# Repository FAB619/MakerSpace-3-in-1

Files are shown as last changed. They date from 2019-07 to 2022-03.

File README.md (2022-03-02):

<div align="center"><h1 style="font-family: courier;" align="center">MakerSpace 3-in-1</h1></div>

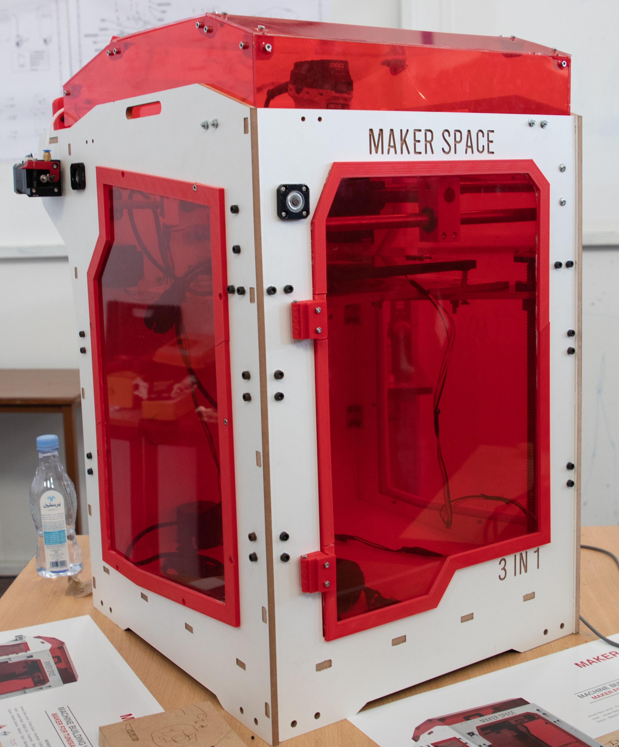
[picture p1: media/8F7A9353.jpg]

<div align="center"><i>Open Source 3-in-1 fabrication machine</i></div>

# Hello World 
# Premises

3D printers are amazing. Unfortunately, they used to be hulking, complicated, expensive, and with limited functions. We’ve been hearing about and experiencing the pain of setting up the difficult-to-use DIY 3D printer kit and being limited by the standard plug-and-play 3D printer. We are hoping to change that. So we came up with an idea: create a 3D printer, which is easy-to-use, expandable for makers, and truly affordable for everyone.

That’s why we designed MakerSpace to be all-in-one.
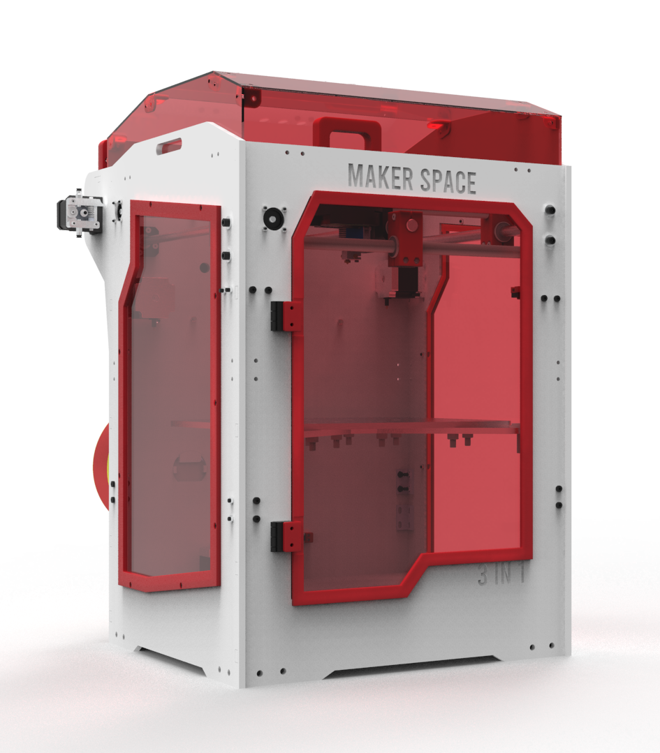
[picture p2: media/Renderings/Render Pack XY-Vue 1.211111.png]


# MakerSpace 3-in-1
MakerSpace is a Combination of 3 machines which characterizes any maker space or fablab around the word,Powerfull tool for rapid prototyping. Designed for Makers, Desingers, Architects ...

 MakerSpace has been developed using standard [Fab Lab equipment](https://docs.google.com/spreadsheets/d/1U-jcBWOJEjBT5A0N84IUubtcHKMEMtndQPLCkZCkVsU/pub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) and [technique](http://fab.academany.org/2019/schedule.html). MakerSpace was built in [FabLab ENIT](https://www.facebook.com/FabLabENIT/) by Kais Alila and the help of a lot of people (Desingers & Engineers).

 MakerSpace brings the advantages of an open source development:

- full awareness about how FabLab machines works
- reproducible design
- possibility to customize the machine and/or to build new ones
- local self-fixing and self-production of the machine parts
- community can use and improve the design
- cheap alternative to have a desktop FabLab
- use MakerSpace as tool for prototyping

Moreover, It's also a desktop makerspace, a combination of 3D printer, laser engraver, and CNC machine with interchangeable heads. Using FDM (Fused Deposition Modeling), it uses standard 1.75mm 3D printer filament with common [e3d v6](https://e3d-online.com/) extruder, 2 watt Laser module with TTl driver usefull for cutting and engraving on paper, cardbord, 3mm MDF and plexiglass and 500 watt spindle for molding and casting, making pcbs and cutting wood.

MakerSpace was designed starting from two major problems:
-Space factor: With makerspace we are replacing 3 machines so we gain have more space.
-Cost factor: With all-in-one machines we are saving money
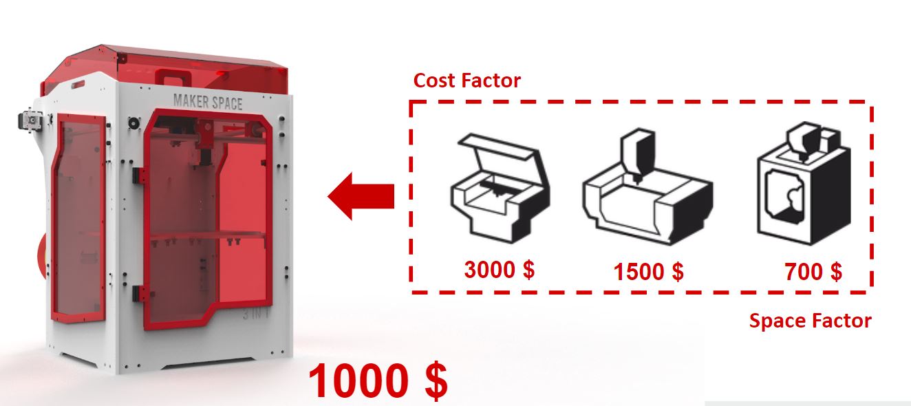
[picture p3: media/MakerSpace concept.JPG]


# Specifications
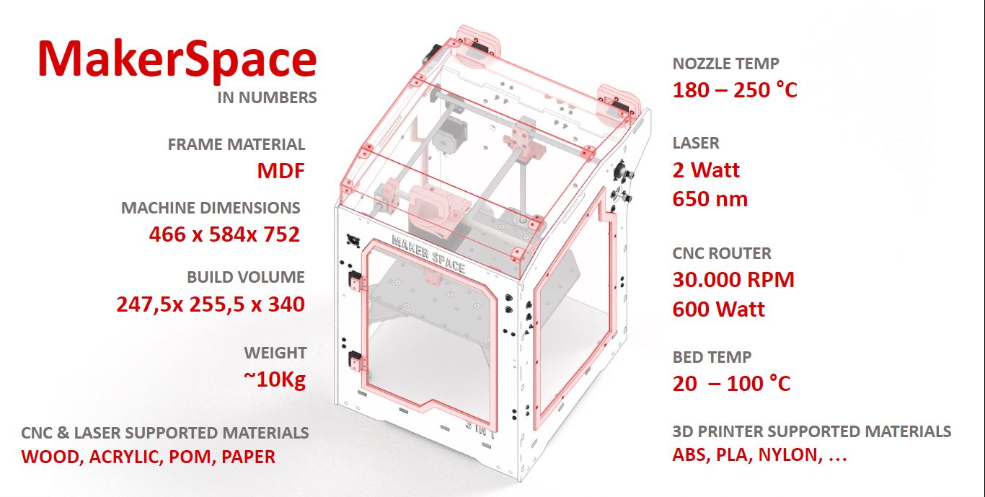
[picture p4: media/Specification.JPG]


**MakerSpace specifications**:

- **466mm x 544mm x 752mm** machine dimension
- **247.5mm x 255.5mm x 340mm** working area
- **3 Tools** with interchangeble tools
- **1.75mm** filament
- **0.1 - 0.6mm** nozzle size
- **NEMA 17-23**  stepper motors
- **BallScrews SFU 1204**
- stages with **linear stainless steel rod guides**
- **Wood frame**
- **heated bed**
- **closed housing** of acrylic (enclouser)
- **2 watt 405nm Laser** module with TTL driver
- **30000 Rpm 500 watt** CNC router (Spindle)
- fabbable **Arduino Mega & Ramps and A4988 stepper driver** based electronics
- **Electronics resolution** 6 microns
- PSU 12V 15A
- printing from **USB** drive
- **Materials**:

    -Plastics: PLA, Flex, ABS, Acetal, Acrylic, PVC…

    -Woods: Oak, Maple, Hickory, Walnut…

    -And much more!
- BOM cost of about **1000€**
- power requirements 220V

# Customizable
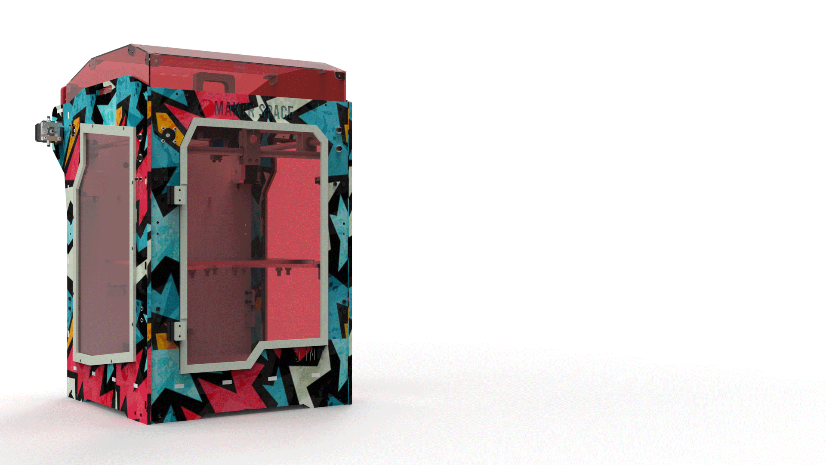
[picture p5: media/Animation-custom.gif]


# Tools
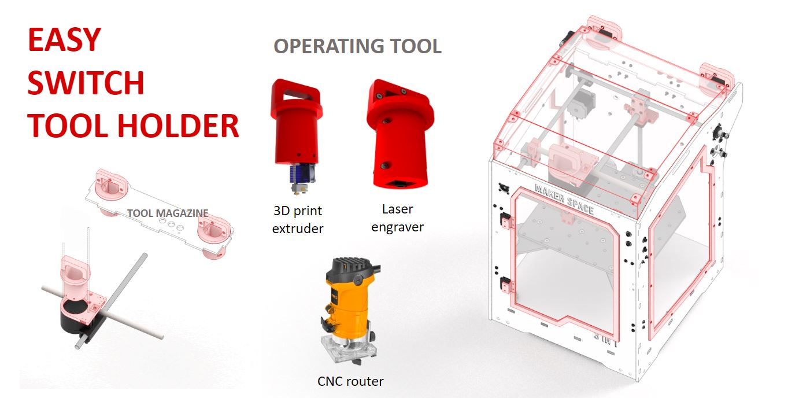
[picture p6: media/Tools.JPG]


# Everything is 3D printed
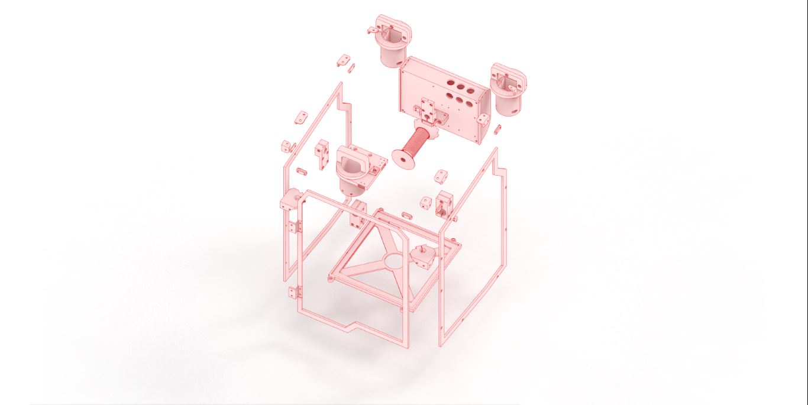
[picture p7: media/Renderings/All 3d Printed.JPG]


To guarantee the reproducibility of MakerSpace, the majority of the parts are 3D printed in Fab Lab. It took approximately 140 hours print, and 2 kilogramms PLA filament. All the parts are designed with solidworks and Simplify3D for generating the g-code. The spool holder is an open source design designed by [Undeviljur](https://www.thingiverse.com/Undeviljur/about) and this is the thingiverse link:

https://www.thingiverse.com/thing:1546811

This is the table for [3D printed Parts](https://github.com/Fab-Lab-Machines/MakerSpace-3-in-1/tree/master/Fabrication/3D%20printing)

|désignation |nombre|build time (hour:minute)|plastic weight (g)|lenght (mm)| |
|---|---|---|---|---|---|
|Box base |1 |13:14:00 |175,15 |5840 | |
|Box-top |2 |18:46:00 |194,86 |64812,3 | |
|Eceres |10 |3:17:00 |31,31 |10412,6 | |
|extruder housing |1 |15:39:00 |254,32 |84588,4 |with support|
|FF_housing |1 |2:14:00 |26,91 |8949,7 |with support|
|Frame-protection-power |2 |6:23:00 |80,49 |26772,2 | |
|Front protection frame |1 |7:14:00 |96,78 |32188,5 | |
|hinge |4 |1:41:00 |16,45 |5472,4 | |
|Laser-housing 1st |1 |7:05:00 |80,07 |26632,7 |with support|
|Laser-housing second |1 |7:06:00 |80,07 |26629,8 |with support|
|LMF_16UU costum |2 |5:00:00 |39,65 |13187,5 | |
|Mors-mobile-extruder |1 |0:41:00 |7,02 |2335 |with support|
|Rod support |1 |1:28:00 |16,02 |5327,7 | |
|Rod support 2 |2 |2:59:00 |32,36 |10762,6 | |
|Spacer_5_10 |4 |0:20:00 |2,25 |746,9 | |
|Support bed & Glass |1 |10:06:00 |121,82 |40517 | |
|support end stop |2 |0:27:00 |4,42 |1470,5 | |
|Support FF For SFU1 |2 |2:02:00 |21 |6985 | |
|Support on Hinge |2 |1:23:00 |14,73 |4899,1 | |
|Support Rod Bottom |2 |3:04:00 |33,01 |10979 | |
|Spool Holder  (all parts)|1 |10:46:00 |123,32 |41015 |with support|
|Tool holder |1 |16:48:00 |191,99 |63855,4 | |
|Tool holder Top |1 |3:51:00 |43,46 |14421,6 | |
|Total : |46 |141:40:00 |1687,46 |508800,9 |

# CNC Milling
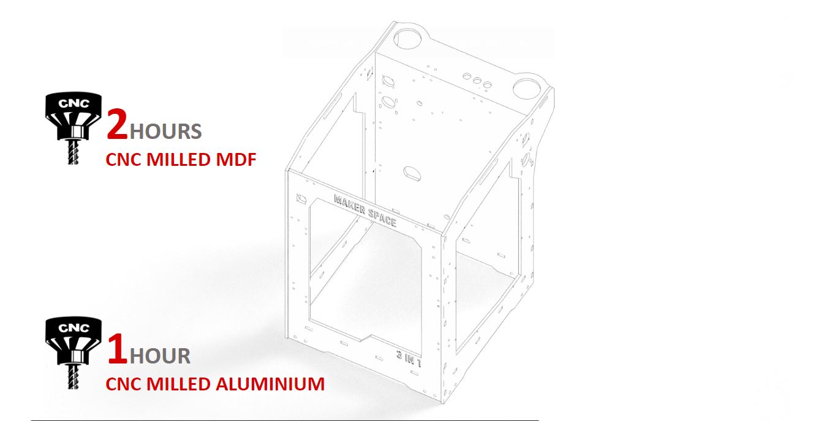
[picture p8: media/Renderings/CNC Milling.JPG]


# Metal parts
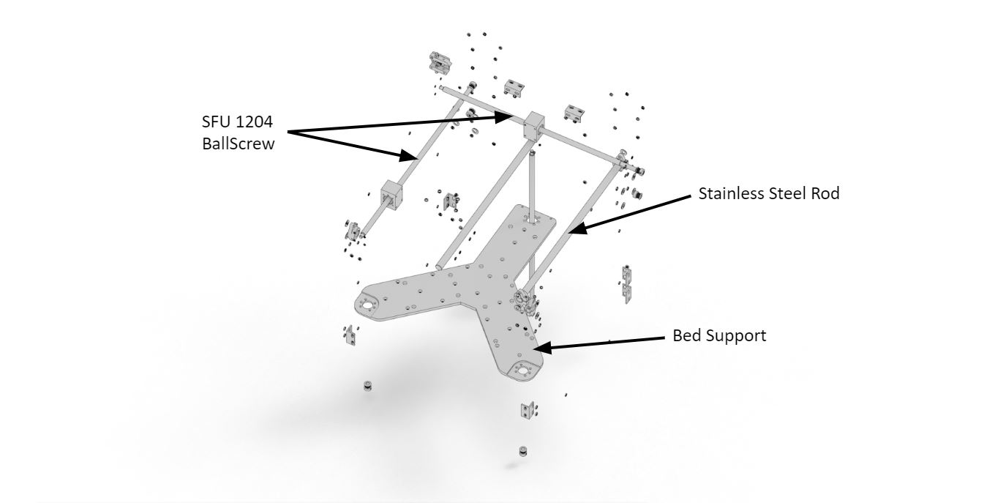
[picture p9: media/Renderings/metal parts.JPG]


# Electronics
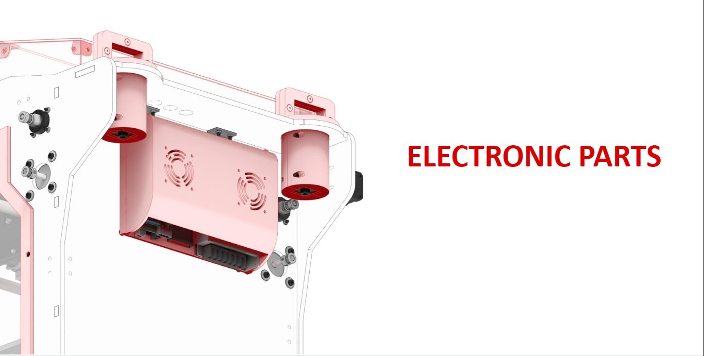
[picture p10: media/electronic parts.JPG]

<div align="center"><i>Electronic Box</i></div>
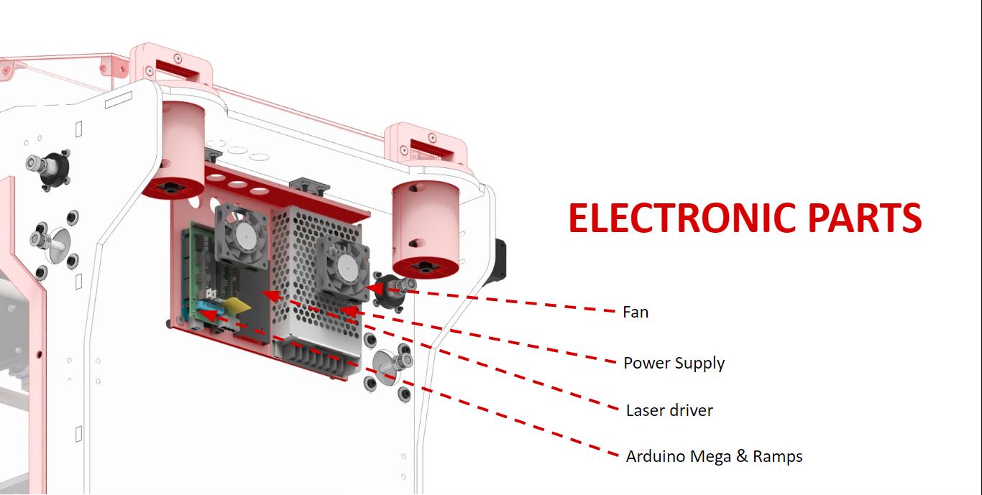
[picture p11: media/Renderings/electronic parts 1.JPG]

<div align="center"><i>Components</i></div>

# Compact design
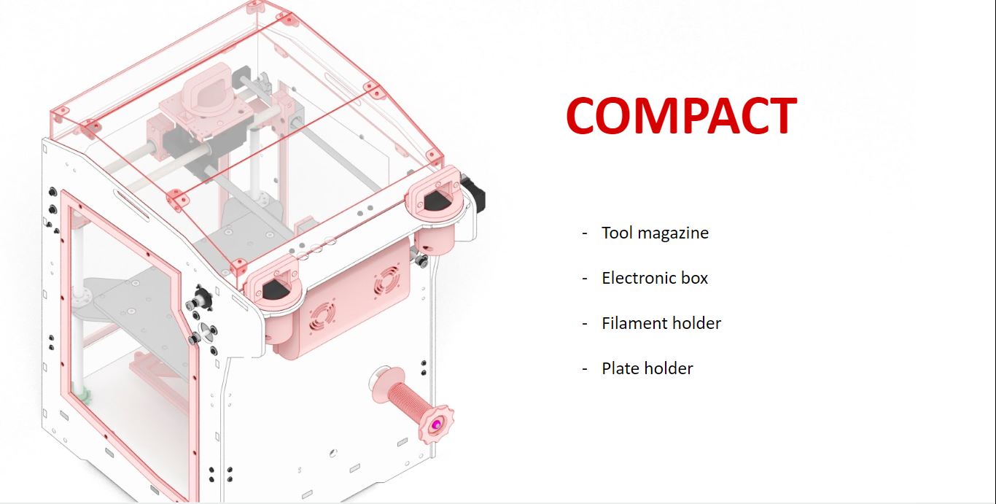
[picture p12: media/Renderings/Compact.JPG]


# Machine Details
You can find clear details in the [docs](https://github.com/Fab-Lab-Machines/MakerSpace-3-in-1/tree/master/Docs) folder in this repository.

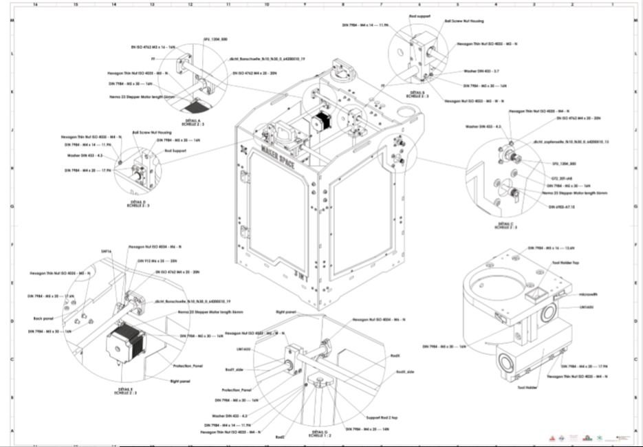
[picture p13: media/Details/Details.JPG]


<div align="center"><i>MakerSpace Details</i></div>

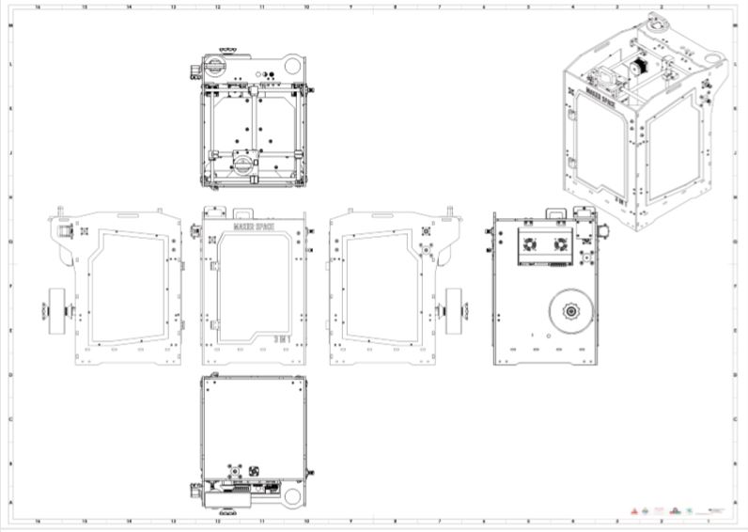
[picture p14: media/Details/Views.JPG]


<div align="center"><i>All Views</i></div>

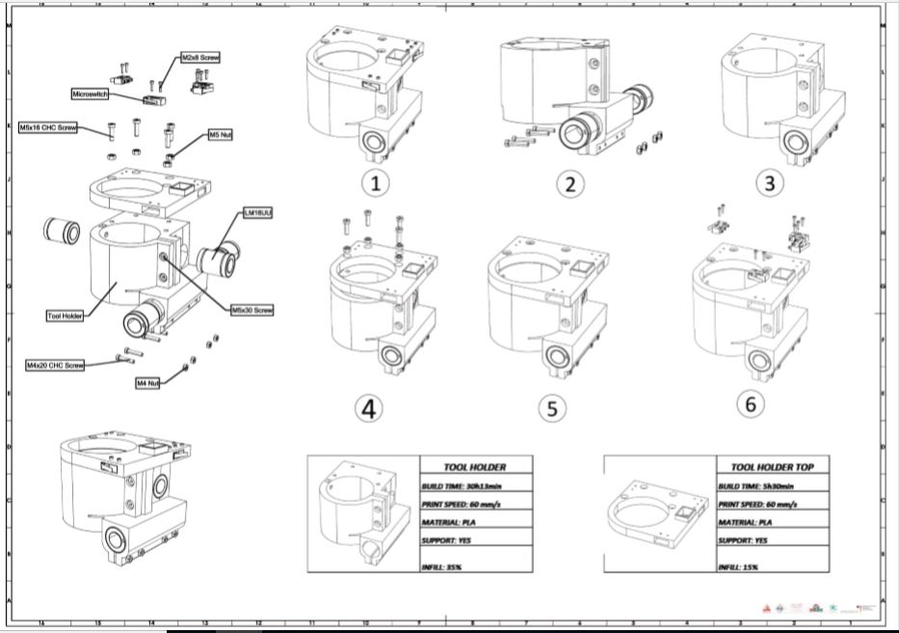
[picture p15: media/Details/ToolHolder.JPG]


<div align="center"><i>Tool Holder Assembly</i></div>

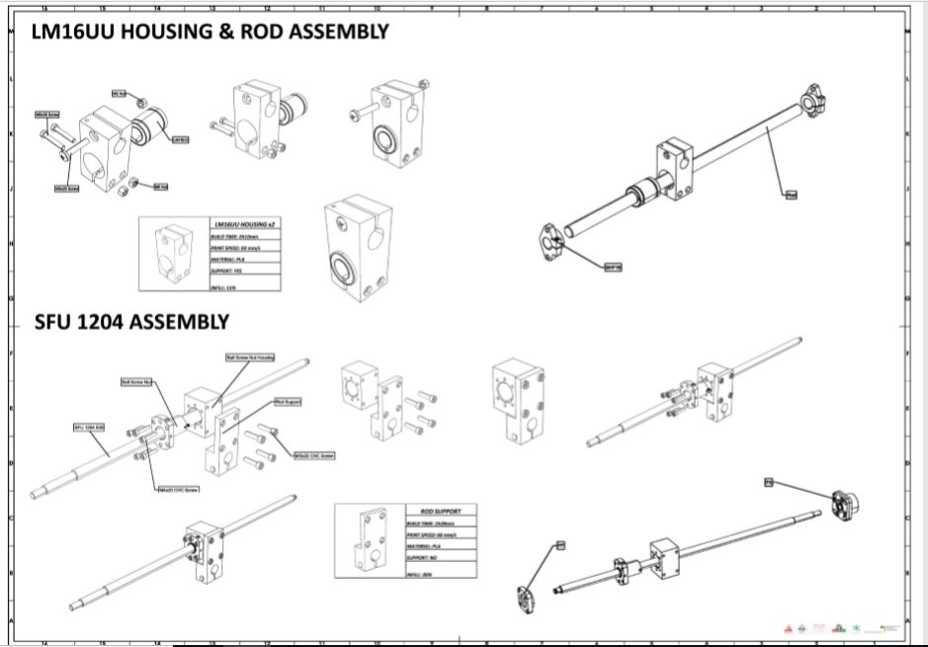
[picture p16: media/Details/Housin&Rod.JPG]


<div align="center"><i>Rod & Housing Assembly</i></div>

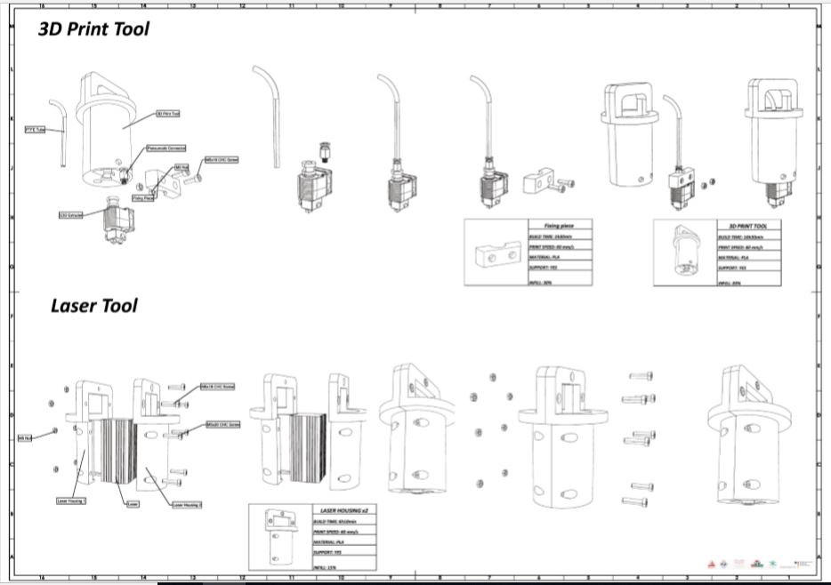
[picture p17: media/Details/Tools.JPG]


<div align="center"><i>Tools Assembly</i></div>

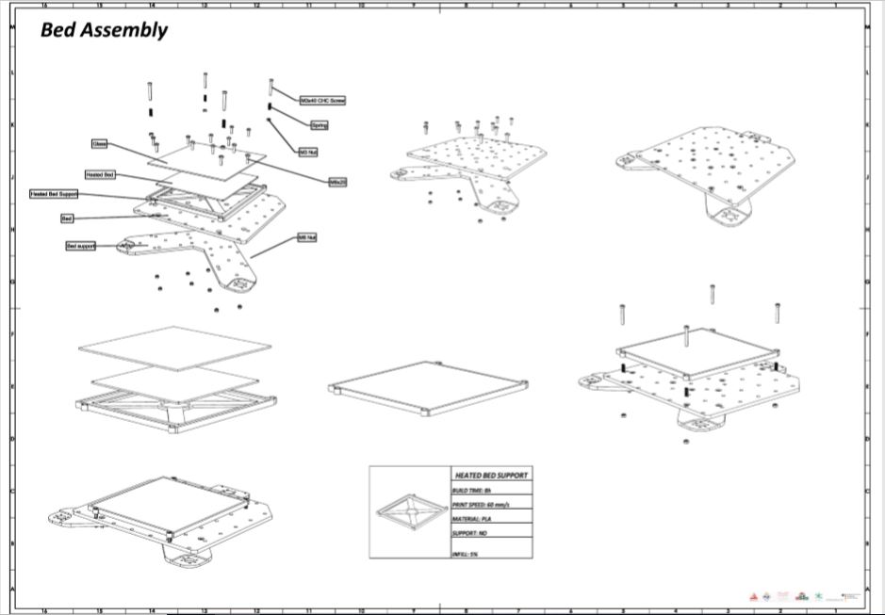
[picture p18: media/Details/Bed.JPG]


<div align="center"><i>Bed Assembly</i></div>

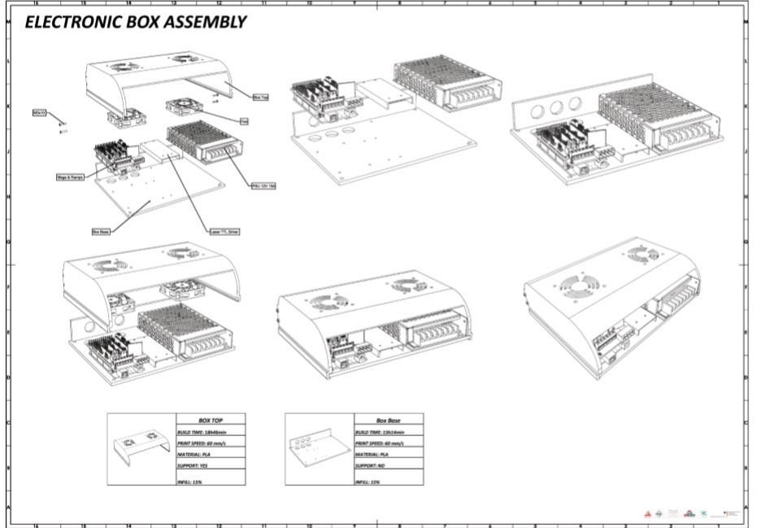
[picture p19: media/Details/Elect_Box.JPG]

<div align="center"><i>Electronic Box Assembly</i></div>

# Software

MakerSpace uses [Marlin Firmware](https://github.com/MarlinFirmware/Marlin) runing on arduino Mega. The configuration changes have been applied into the configuration.h file, you can find it into the [configuration](https://github.com/Fab-Lab-Machines/MakerSpace-3-in-1/tree/master/Config) folder. The most important modification into the code are for laser and CNC (if we use a variable spindle). To use MakerSpace as laser, you need to connect the laser driver ttl pin to a PWM pin from the ramps (Arduino). To do that I suggest using pin 44 (See AUX-2 from ramps) defined as FAN_Pin and control the laser like a fan or  to define pin 6 as the second fan just add this line to Configuration.h:

- **#define** FAN1_PIN 6 // 2nd fan output attached to laser TTL input

You can then control the laser from your G-code using M106 P1, like so…:

- **M106 P1 S0**   ; Laser off (P1 = 2nd fan output)

- **M106 P1 S128** ; Laser at 50%

- **M106 P1 S255** ; Laser at 100%

**NOTE**: You can use Fan0 if it is available, in which case you will not need to define the above. As of this edit, Marlin can control up to 3 fans via M106/M107. The same commands for variabble spindle (Still need to test)

For CNC Cutting or engraving, we use Fusion 360 to generate the g code using GRBL as post process.

# MakerSpace: Laser Cutting/Engraving
As laser cutter and engraver machine, MakerSpaceis is equiped with 2 watt laser usefull for cutting papers, 3mm wood, 3mm acrylic and engrave on it.
To Generate the G-code, there are diffrent softwares and methods.

The first test for laser was generated using inkscape and [JTP laser tool plug-in](https://jtechphotonics.com/?page_id=2012) realy usefull and easy interface & the g-code generated is compatible with Marlin Firmware.
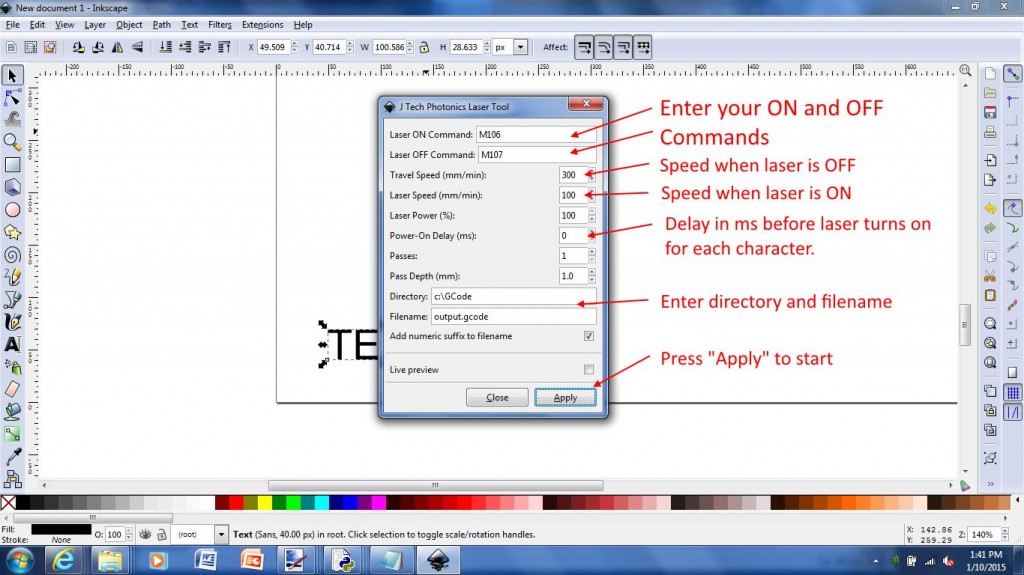
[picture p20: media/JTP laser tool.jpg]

<div align="center"><i>(https://jtechphotonics.com/?page_id=1980)</i></div>

The second software tested was [LaserGRBL](http://lasergrbl.com/en/) which is one of the best Windows GCode streamer for DIY Laser Engraver. LaserGRBL is able to load and stream GCode path to arduino, as well engrave images, pictures and logo with internal conversion tool. (more details the website)
we used this software to test image engraving and it is also compatible with Marlin Firmware with some modifications.
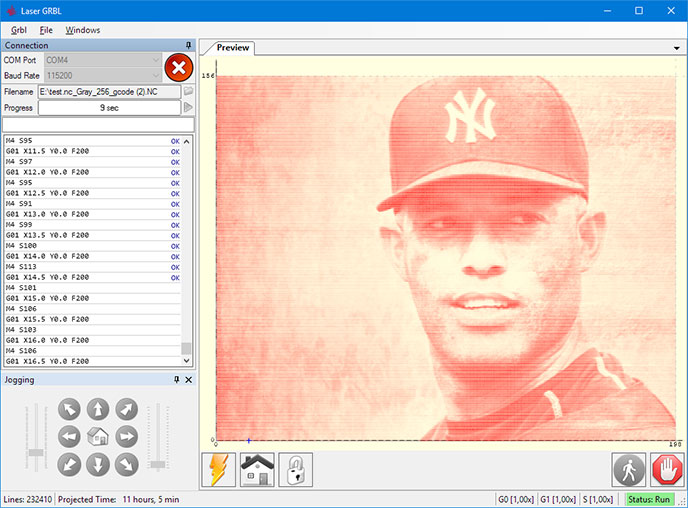
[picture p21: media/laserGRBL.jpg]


# Build your own MakerSpace

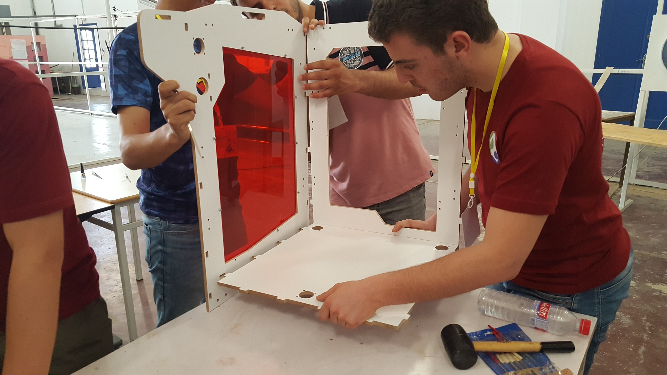
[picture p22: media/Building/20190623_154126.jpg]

MakerSpace is made by using a mix of fabricated and ready-made parts. The ready-made parts are selected to be as common/standard as possible, to make the sourcing of them easy in many countries. For both the raw materials needed for the fabricated parts, and the ready-made parts, refer to the Bill-of-Material for details:

**[MakerSpace BOM](https://github.com/Fab-Lab-Machines/MakerSpace-3-in-1/blob/master/Docs/MakerSpace_BOM%20-%20Feuille%201.pdf)**

The fabrication of the parts mainly relays on standard [Fab Lab equipment](https://docs.google.com/spreadsheets/d/1U-jcBWOJEjBT5A0N84IUubtcHKMEMtndQPLCkZCkVsU/pub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). It will be therefore possible to make MakerSpace in any of Fab Labs worldwide having it. Below a list of the required tools and machines:

- C02 laser cutter:
 - able to cut 3mm acrylic
- large format wood CNC machine:
 - ShopBot or similar, size 2500x1250mm
 - to machine the aluminum parts (bed, Z axis supports)
 - to machine the 8mm MDF parts (frame)
- 3D printer:
 - a small one (30x30x30cm) is sufficient
 - to print all 3D printed parts
- Lathe:
 - To turn two SFU 1204 ball screw
 - to turn some aluminum parts (Baguge for steppers)
- standard set of tools:
 - spanner key set
 - hex key set
 - DIN 875
 - calipers
 - screwdriver set
 - player set (grabber/cutter etc..)
 - rubber hummers

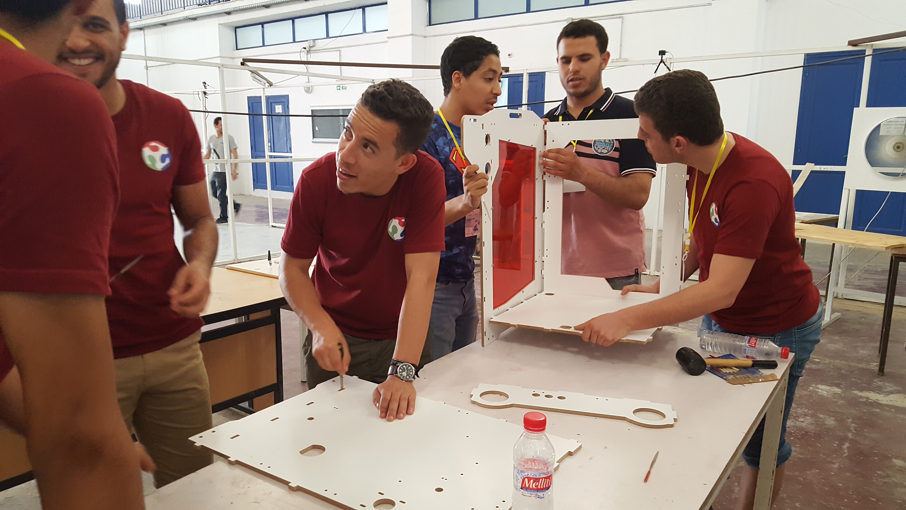
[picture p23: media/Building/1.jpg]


All MakerSpace parts have been modeled Solidworks and all the files are in [CAD](https://github.com/Fab-Lab-Machines/MakerSpace-3-in-1/tree/master/CAD) folder . Using Solidworks is possible to export/prepare the parts for production in the following ways:

- right click save as STL, on a body that needs to be 3D printed
- right click export as DXF, for laser cutting

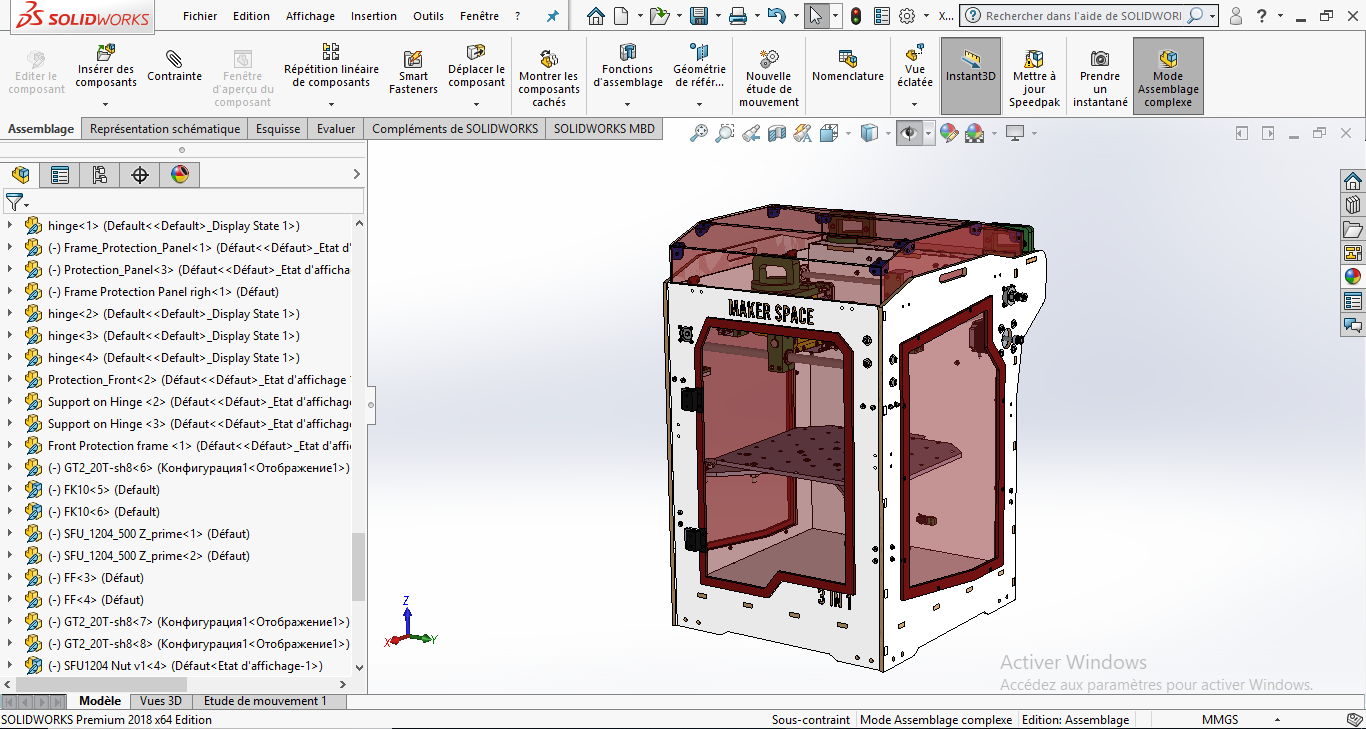
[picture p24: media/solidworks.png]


For more details about the tools and once you have all the fabricated parts available, refer to the for step-by-step assembly instructions and tips: **[MakerSpace Building Manual](https://github.com/Fab-Lab-Machines/MakerSpace-3-in-1/wiki)**

# Media

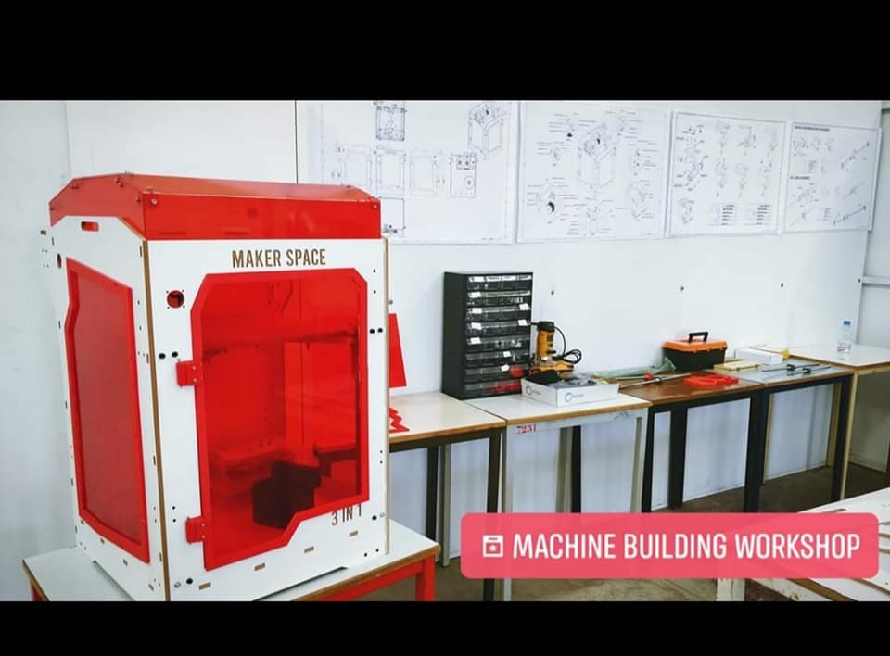
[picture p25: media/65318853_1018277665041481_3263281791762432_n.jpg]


**MakerSpace laser engraving at [Fab Lab ENIT](https://www.facebook.com/FabLabENIT/)** "**Makers for tunisia: Machine building workshop**"
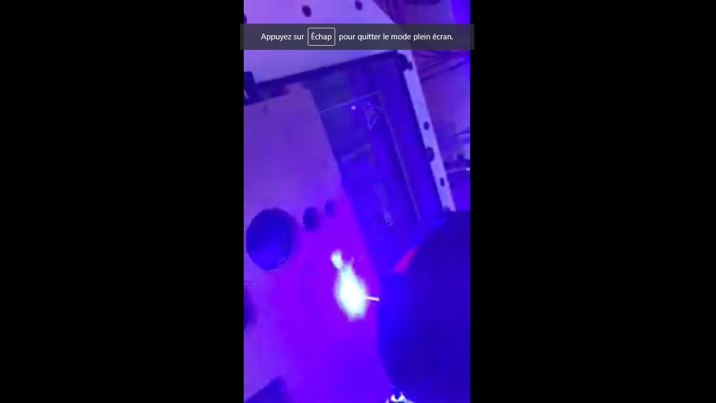
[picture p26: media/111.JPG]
[](https://www.youtube.com/watch?v=vwQPz8xjFZ0&feature=youtu.be)

# Contact

- **alilakais@gmail.com**
- **[Linkedin](https://www.linkedin.com/in/kais-alila-3a1b35163/)**

# Acknowledgements

The development of this machine has been funded by:<br>
**[German Federal Ministry of Education and Research](https://www.bmbf.de/en/index.html)**

Funds implemented by:<br>
**[OpenLab Hamburg](http://openlab-hamburg.de/startpage/)**<br>
[Helmut-Schmidt-Universität Universität der Bundeswehr](https://www.hsu-hh.de/en/)<br>
Laboratorium Fertigungstechnik<br>
Holstenhofweg 85<br>
22043 Hamburg<br>

# License

<br />MakerSpace is licensed under a <a rel="license" href="http://creativecommons.org/licenses/by-sa/4.0/">Creative Commons Attribution-ShareAlike 4.0 International License</a>.
# Note
This documentation will be continuously improved as soon there are updates and/or improvements on the machine.

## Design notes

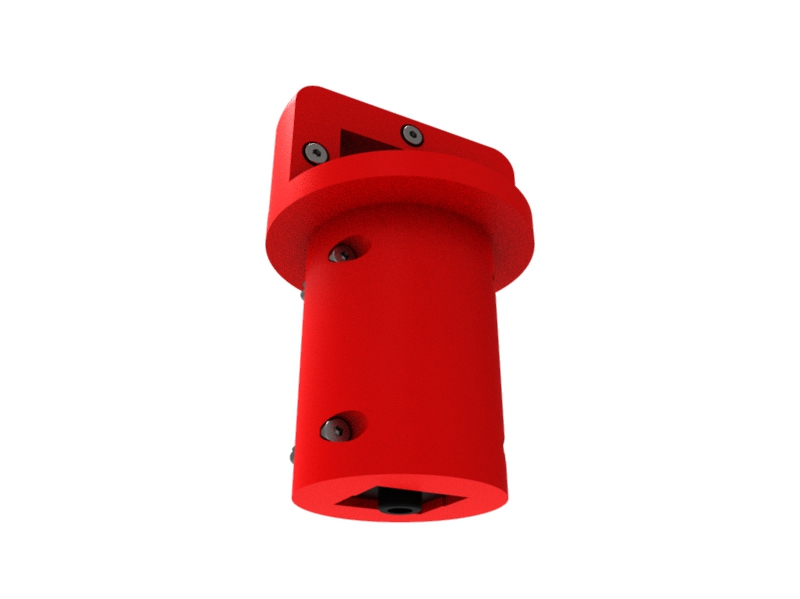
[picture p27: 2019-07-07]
media/laser tool.jpg

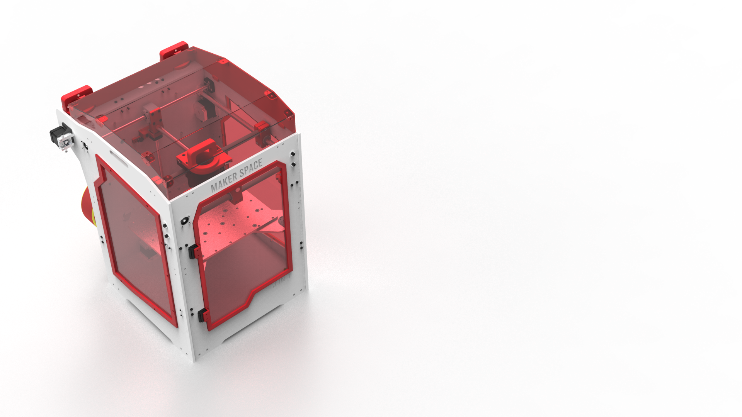
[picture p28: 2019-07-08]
media/Renderings/Render Pack XY-Vue 2.22.png

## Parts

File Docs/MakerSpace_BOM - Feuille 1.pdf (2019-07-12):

Item | Part Number | Link | Amount | Unit cost (euro) | Total cost (euro) | TOTAL (EUR)
Nema 23 | 23HS8430 | Link (https://www.amazon.de/gp/product/B01CYIU0EG/ref=ox_sc_act_title_25?smid=A3VDDHTQKR2D2E&psc=1) | 3 | 22,41 € | 67,23 € | 1 041,80 €
Nema 17 | - | Link (https://www.amazon.de/gp/product/B07RQCQDZP/ref=ox_sc_act_title_24?smid=A1Z13FT0FSYVKD&psc=1) | 1 | 13,69 € | 13,69 €
Ramps Kit : Arduino Mega / 5 drv8825 /jumpers | - | Link (https://www.amazon.de/gp/product/B01C3I27KC/ref=ox_sc_act_title_12?smid=A1BTLUV6GKJM47&psc=1) | 1 | 43,99 € | 43,99 €
E3D extruder V6 | - | Link (https://www.amazon.de/gp/product/B078SLDBY3/ref=ox_sc_act_title_21?smid=A1O0D8SJPA8CHD&psc=1) | 1 | 15,29 € | 15,29 €
Heated Bed Mk3 | - | Link (https://www.amazon.de/gp/product/B0742KS8QY/ref=ox_sc_act_title_11?smid=A30L2KD589ZCAC&psc=1) | 1 | 16,98 € | 16,98 €
End stops Kit 3pcs | - | Link (https://www.amazon.de/gp/product/B07BXNL767/ref=ox_sc_act_title_14?smid=A2HSFPQG9EH8HP&psc=1) | 2 | 4,99 € | 9,98 €
NTC 3950 100K 1% Thermistor Temp Sensor | - | Link (https://www.amazon.de/gp/product/B071RQ1945/ref=ox_sc_act_title_10?smid=A13ZJ94CYI3F7Y&psc=1) | 1 | 4,59 € | 4,59 €
Power Supply 12V 15A | - | Link (https://www.amazon.de/gp/product/B019JUVYZG/ref=ox_sc_act_title_13?smid=A25HL4JIED5BM8&psc=1) | 1 | 30,46 € | 30,46 €
Wires 3 pin 70cm | - | Link (https://www.amazon.de/gp/product/B07NQ5CYL7/ref=ox_sc_act_title_1?smid=A1ZC5C07TAPOD5&psc=1) | 1 | 5,01 € | 5,01 €
Wires 4 pin 100cm | - | Link (https://www.amazon.de/gp/product/B07PZSGTPW/ref=ox_sc_act_title_2?smid=A26XO19FELV3Y9&psc=1) | 1 | 3,56 € | 3,56 €
Laser Module 2.5W 405nm + Protection glasses | - | Link (https://www.amazon.de/gp/product/B07QJ5DC71/ref=ox_sc_act_title_4?smid=A31O6TRJ33P95X&psc=1) | 1 | 79,90 € | 79,90 €
Router Trimmer 710w Variable speed | - | Link (https://www.amazon.de/gp/product/B07BGVK7G2/ref=ox_sc_act_title_7?smid=AO3TA36ZY3VEZ&psc=1) | 1 | 45,00 € | 45,00 €
Mk8 Extruder | - | Link (https://www.amazon.de/gp/product/B07QW4YF5B/ref=ox_sc_act_title_23?smid=A2XXYTY5NMDPP3&psc=1) | 1 | 13,99 € | 13,99 €
Mount for nema17 | - | Link (https://www.amazon.de/gp/product/B07Q7FYC6R/ref=ox_sc_act_title_22?smid=A3I29TEWZGDKTG&psc=1) | 1 | 3,97 € | 3,97 €
Pulley GT2 20T 8mm | - | Link (https://www.amazon.de/gp/product/B01F3IAE5O/ref=ox_sc_act_title_15?smid=A30L2KD589ZCAC&psc=1) | 8 | 3,12 € | 24,96 €
Timming belt GT2 200mm | - | Link (https://www.amazon.de/gp/product/B07G4M83BH/ref=ox_sc_act_title_16?smid=A2HSFPQG9EH8HP&psc=1) | 2 | 2,99 € | 5,98 €
Timming belt GT2 5000mm | - | Link (https://www.amazon.de/gp/product/B06Y5ZJRK9/ref=ox_sc_act_title_17?smid=A208YHQS1HBK9E&psc=1) | 1 | 8,99 € | 8,99 €
SHF16 kit (2pcs) | - | Link (https://www.amazon.de/gp/product/B07SCXR86H/ref=ox_sc_act_title_18?smid=AQ1IBDB6G2RRD&psc=1) | 2 | 6,34 € | 12,68 €
STainless steel rod 16mmx3000m | - | Local | 1 | 34,37 € | 34,37 €
LM16UU 2per pack | - | Link (https://www.amazon.de/gp/product/B07J9NWJGH/ref=ox_sc_act_title_9?smid=AQ1IBDB6G2RRD&psc=1) | 4 | 6,59 € | 26,36 €
L Bracket | - | Link (https://www.amazon.de/gp/product/B07SPSKLX2/ref=ox_sc_act_title_3?smid=A3O1QMMJ5A2UUZ&psc=1) | 10 | 3,60 € | 36,00 €
8mm MDF 2mx3m | - | Local | 1 | 28,10 € | 28,10 €
Red Plexiglass 2mx1m | - | Local | 1 | 75,00 € | 75,00 €
Protection glasses 400nm-450nm | - | Link (https://www.amazon.de/400nm-450nm-Violett-Laser-Schutzbrille-Brillen/dp/B07B8HN819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) | 2 | 16,58 € | 33,16 €
FK10/FF10 for SFU 1204 | - | Link (https://www.amazon.de/gp/product/B019MLAVFQ/ref=ox_sc_act_title_26?smid=A1M2R6SRAKXB53&psc=1) | 5 | 23,49 € | 117,45 €
SFU 1204 500mm | - | Link (https://www.amazon.de/gp/product/B07FVV6PVG/ref=ox_sc_act_title_27?smid=A3MWTOW3Y5FBF1&psc=1) | 5 | 32,59 € | 162,95 €
PLA Red 1Kg | - | Link (https://www.amazon.de/gp/product/B078SG1QWM/ref=ox_sc_act_title_19?smid=A1JIK30NYBE0YF&psc=1) | 1 | 20,99 € | 20,99 €
PLA Black 1Kg | - | Link (https://www.amazon.de/gp/product/B078SGFV3C/ref=ox_sc_act_title_20?smid=A1JIK30NYBE0YF&psc=1) | 1 | 19,90 € | 19,90 €
PTFE Tube 1.75 | - | Link (https://www.amazon.de/Teflon-Schlauch-schwarz-D%C3%BCsenextruder-Pritner-durchsichtig/dp/B07SH658BC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) | 1 | 3,06 € | 3,06 €
Emergency Stop | - | Link (https://www.amazon.de/ZCHXD-Emergency-Station-Mushroom-Locking/dp/B07SLVNSG7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) | 1 | 9,62 € | 9,62 €
Screws, washers | - | Local | 1 | 60,00 € | 60,00 €
608zz Ball bearings 8per pack | - | Link (https://www.amazon.de/Skateboard-Kugellager-Longboard-Rollschuhen-Abgeschirmt/dp/B01N1MX8R0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) | 1 | 8,59 € | 8,59 €

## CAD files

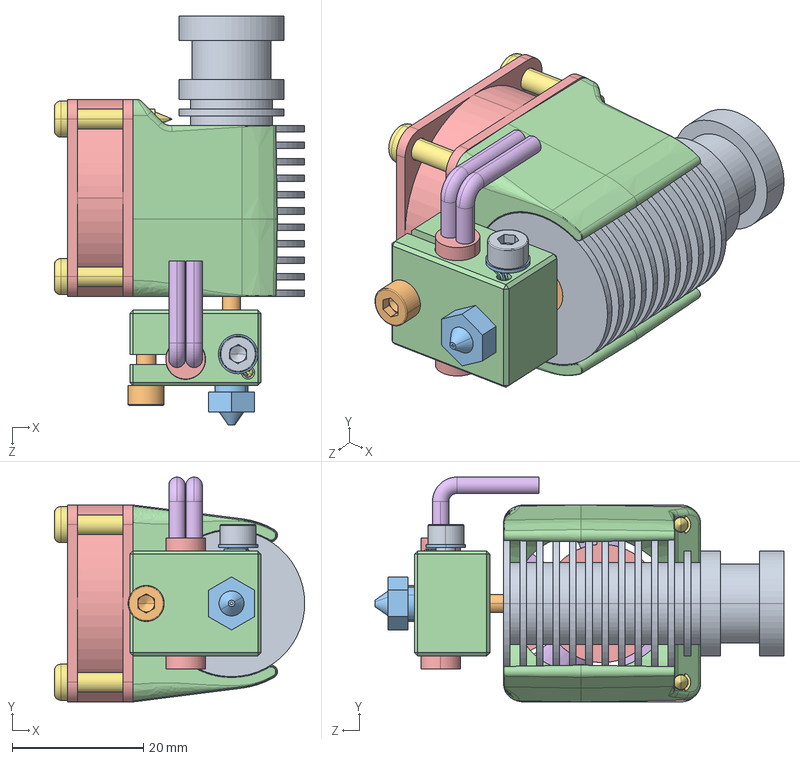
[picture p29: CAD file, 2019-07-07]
CAD/3DPrint_Tool/e3d-all-metal-hotend-v6-1.snapshot.2/E3D All Metal Hotend V6 assy.STEP
38.1 x 34.3 x 62.3 mm
E3D v6 HotEnd - Heatsink
E3D v6 HotEnd - Heatbreak
E3D v6 HotEnd - Nozzle
E3D v6 HotEnd - Heat Block
Ceramic Cartridge Heater
Thermistor
HEXAGON SOCKET HEAD CAP SCREWS_SCB3-4
HEXAGON SOCKET HEAD CAP SCREWS_SCB3-10
Flat Washers_PWF3
E3D-v6 Fan Duct
Fan-House-30x30x10-Promoco_Fan-House-KDE0503PFB3-Promoco
Fan-30x30x10-Promoco_Fan-KDE0503PFB3-Promoco
Self Tapping Screws - Pan Head_CSPTRSA-SUS-TP3-16 x 4

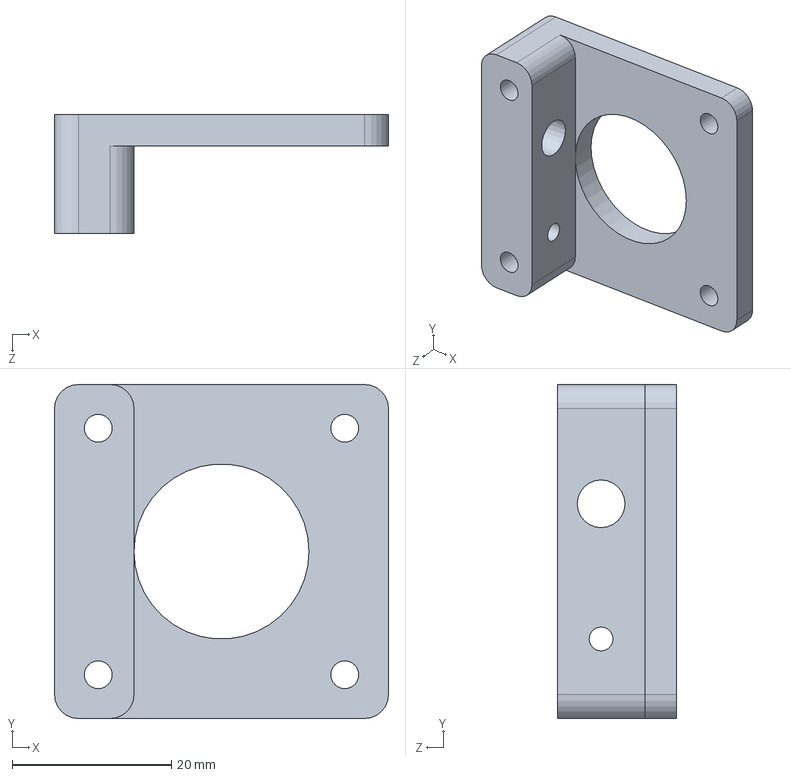
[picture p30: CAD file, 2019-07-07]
CAD/3DPrint_Tool/xgentec-bowden-extruder-1.snapshot.2/Main Block.SLDPRT
42.0 x 42.0 x 15.0 mm

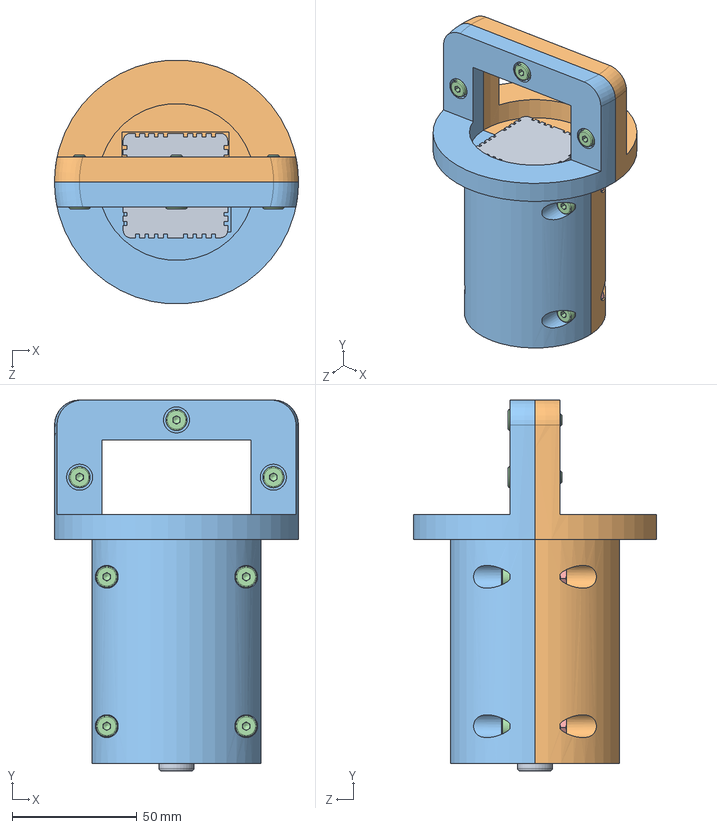
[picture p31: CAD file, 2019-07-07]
CAD/Laser_Tool/Laser_Tool.SLDASM
98.0 x 149.0 x 97.8 mm
Laser
Laser_Housing_1st
Laser_Housing_2second
socket head thin cap screw_din22 x 7
hex thin nut chamfered gradeab_din x 7

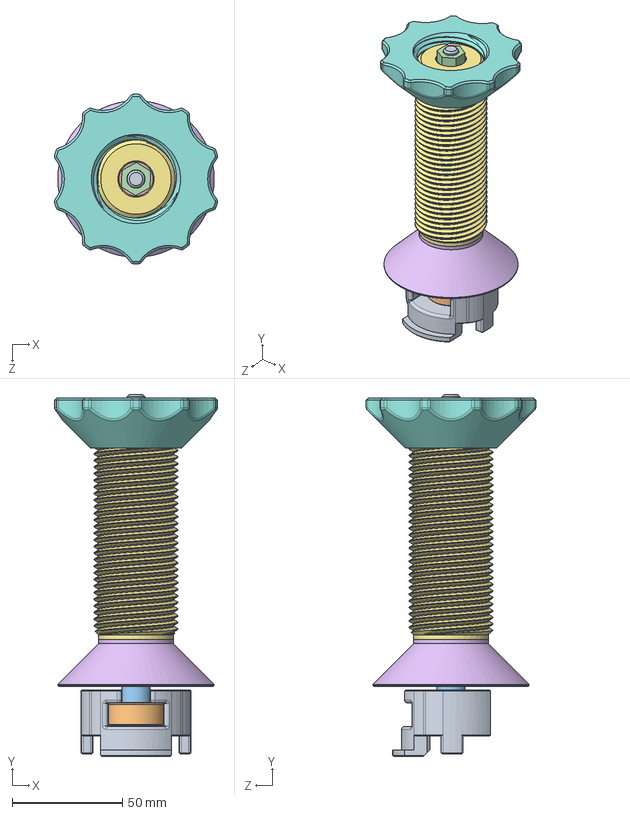
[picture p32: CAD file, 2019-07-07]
CAD/3DPrint_Tool/Spool holder/Solidworks_files_V2/Spool Holder V2.SLDASM
74.1 x 164.3 x 77.0 mm
Printer mount V2
T-piece
Short Tube V2
M8 Nut x 2
Plastic Bearing x 2
Threaded Cone V2
Threaded Tube
Spool Nut
M8 threaded rod
Long Tube V2

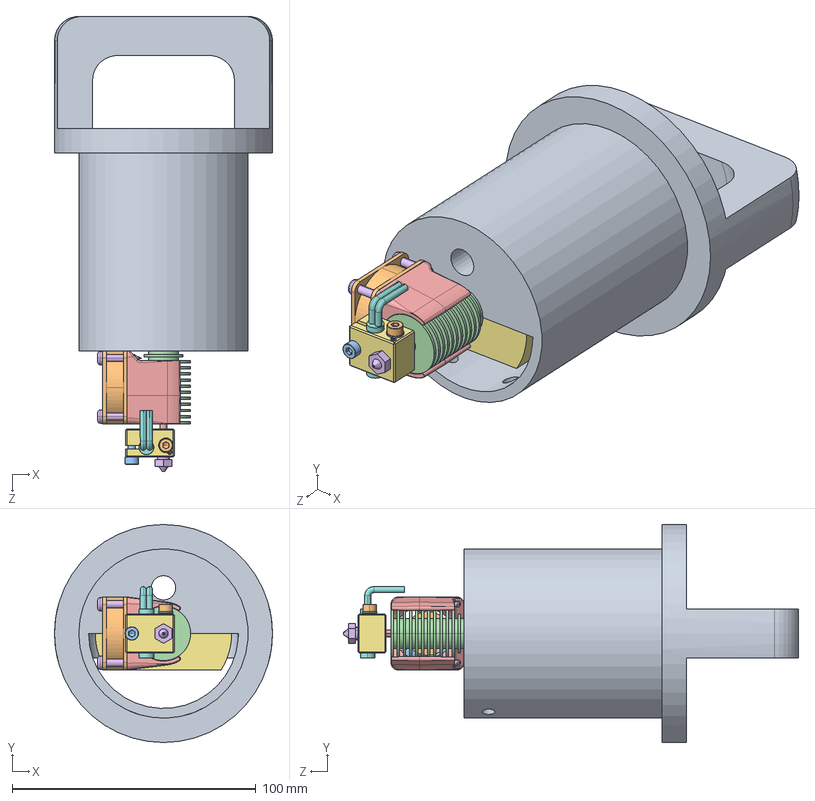
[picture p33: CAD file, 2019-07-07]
CAD/3DPrint_Tool/3DPrint_tool.SLDASM
89.5 x 89.5 x 186.9 mm
Extruder Housing
Fan-House-30x30x10-Promoco_Fan-House-KDE0503PFB3-Promoco.STEP
Fan-30x30x10-Promoco_Fan-KDE0503PFB3-Promoco.STEP
E3D v6 HotEnd - Heatsink.STEP
E3D v6 HotEnd - Heatbreak.STEP
E3D v6 HotEnd - Nozzle.STEP
E3D v6 HotEnd - Heat Block.STEP
Ceramic Cartridge Heater.STEP
Thermistor.STEP
HEXAGON SOCKET HEAD CAP SCREWS_SCB3-4.STEP
HEXAGON SOCKET HEAD CAP SCREWS_SCB3-10.STEP
Flat Washers_PWF3.STEP
E3D-v6 Fan Duct.STEP
Self Tapping Screws - Pan Head_CSPTRSA-SUS-TP3-16.STEP x 4
Mors Mobile_Extruder
Pneumatic Connector

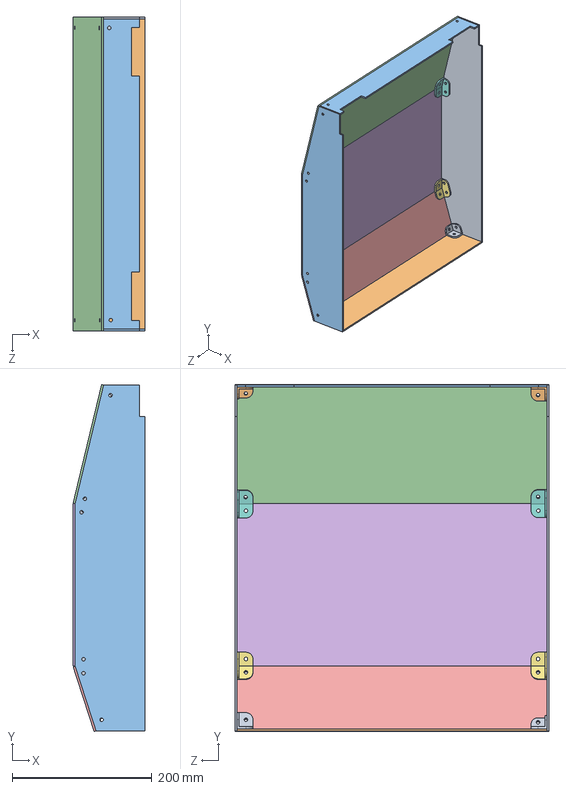
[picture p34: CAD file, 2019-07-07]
CAD/Enclouser/Enclouser1.SLDASM
103.0 x 496.9 x 450.3 mm
Enclouser _Left_Right
Front
Back
incline_big
incline_Small
top
Ecerres-For-Small x 2
Ecerre_for_big x 2
Ecerre_coin small x 2
Ecerre_coin_big x 2
Enclouser _Left

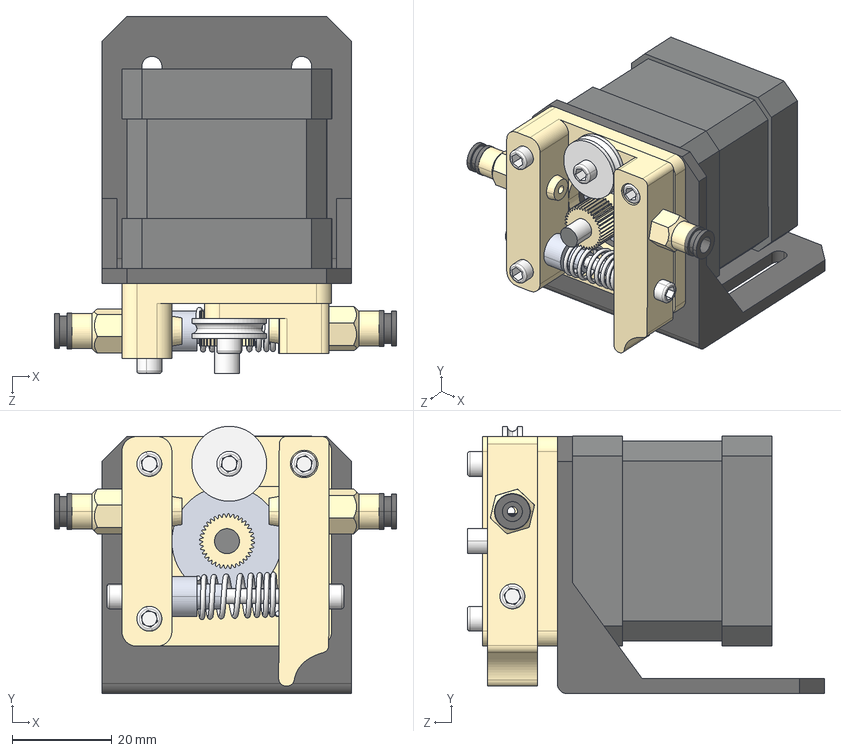
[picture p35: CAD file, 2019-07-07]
CAD/Bowden Assembly.STEP
68.5 x 53.5 x 71.5 mm
Main Block
Arm
Feed Bearing
PTFE 4mm Fitting x 2
Adjust Mount
Compression Spring
Bowden LBracket
Bowben Nema 17
Hex M3x22 x 2
Hex M3x25
Hex M3x20
Toothed Filament Feed
Hex M3x6
Hex M3x15

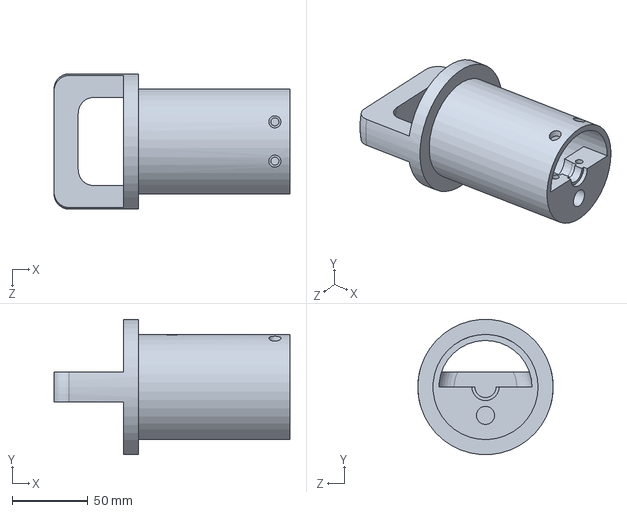
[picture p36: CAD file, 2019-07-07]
CAD/3DPrint_Tool/Extruder Housing final.SLDPRT
156.0 x 89.2 x 89.5 mm

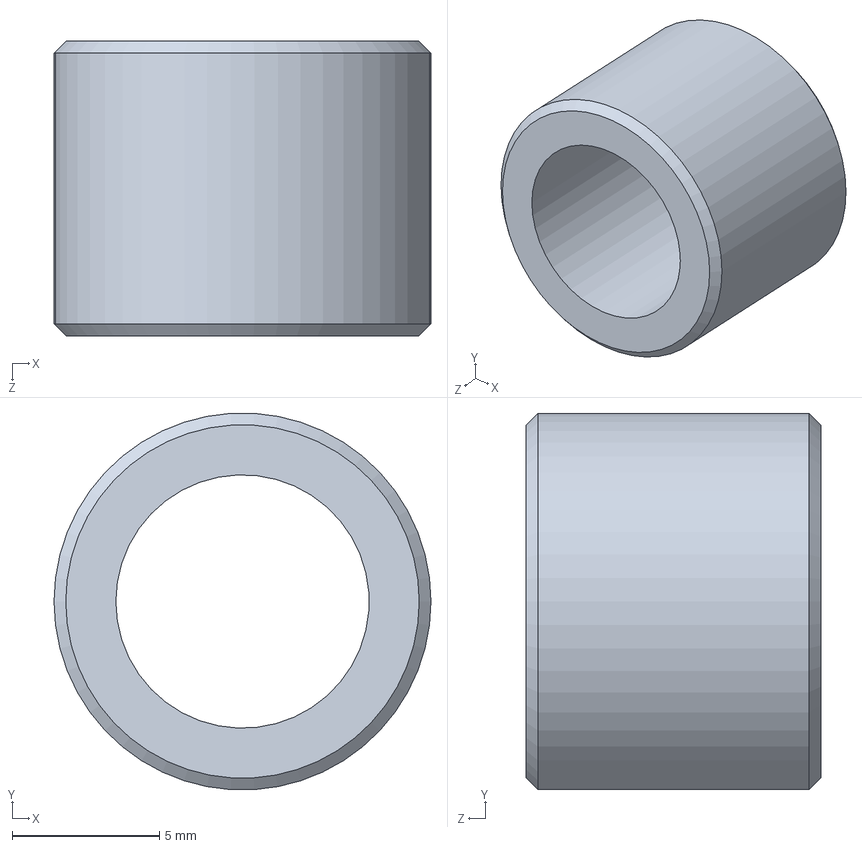
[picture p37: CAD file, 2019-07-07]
CAD/3DPrint_Tool/Spool holder/Solidworks_files_V2/Short Tube V2.SLDPRT
12.8 x 12.8 x 10.0 mm

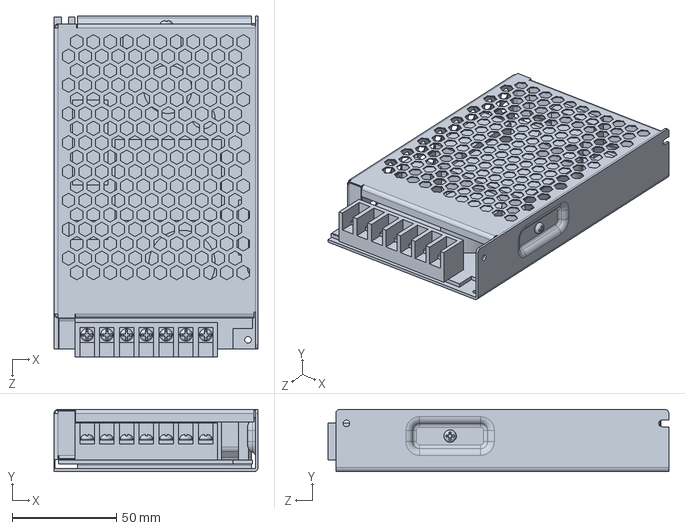
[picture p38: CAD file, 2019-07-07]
CAD/electronic box/Power Supply 12V 10A.SLDPRT
98.0 x 30.0 x 163.7 mm

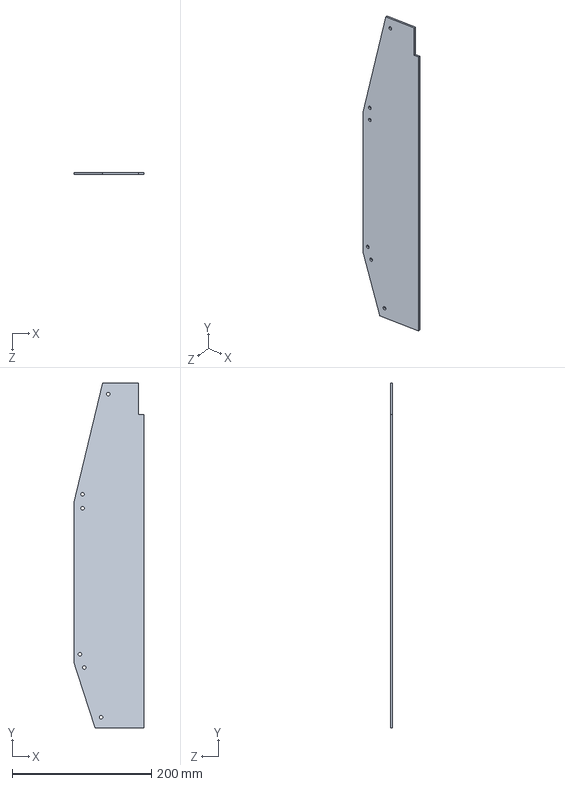
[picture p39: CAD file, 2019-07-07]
CAD/Enclouser/Enclouser _Left_Right.SLDPRT
100.0 x 495.3 x 3.00 mm

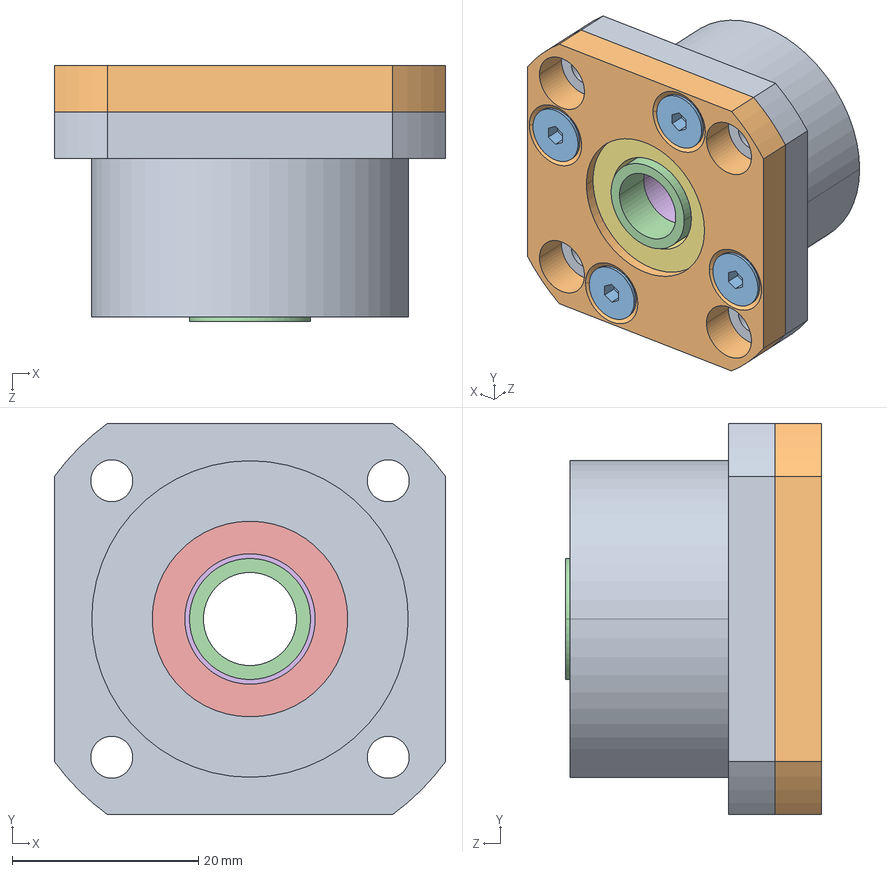
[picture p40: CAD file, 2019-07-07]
CAD/FK10.STEP
42.0 x 42.0 x 27.5 mm
_gehaeuse_fk_0_64200510_2
_gehaeuseflnasch_fk10_fk30_0_64200510_4
_schr_fk10_fk30_0_64200510_6 x 4
_buchse_fk_0_64200510_11 x 2
_dicht_zapfenseite_fk10_fk30_0_64200510_13
_lager_fk_0_64200510_15 x 2
_dicht_flanschseite_fk10_fk30_0_64200510_19

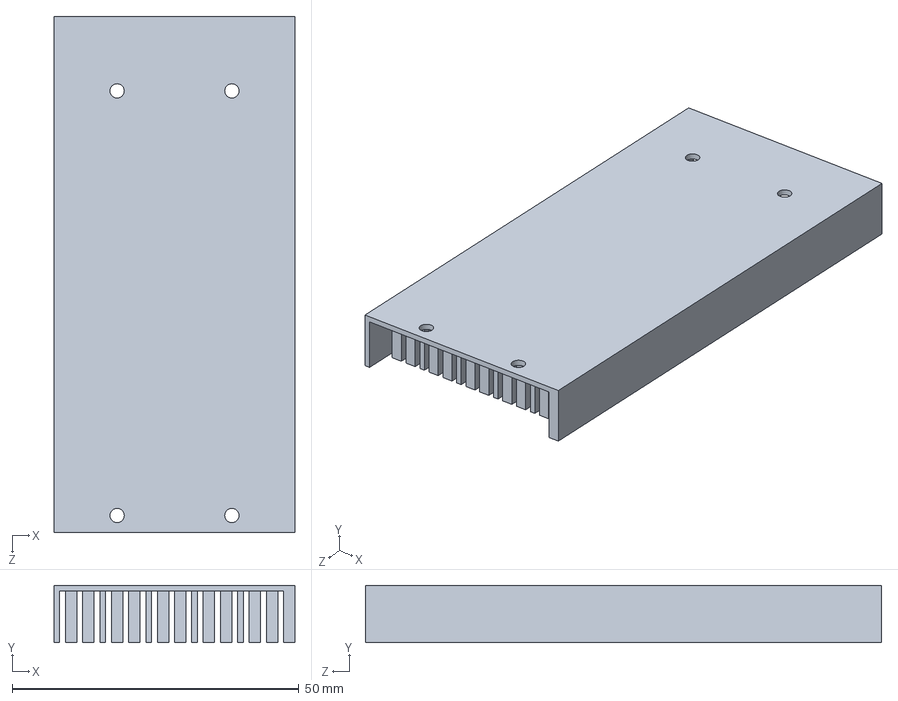
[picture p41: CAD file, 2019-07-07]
CAD/Laser_Tool/Driver support.SLDPRT
42.0 x 10.0 x 90.0 mm

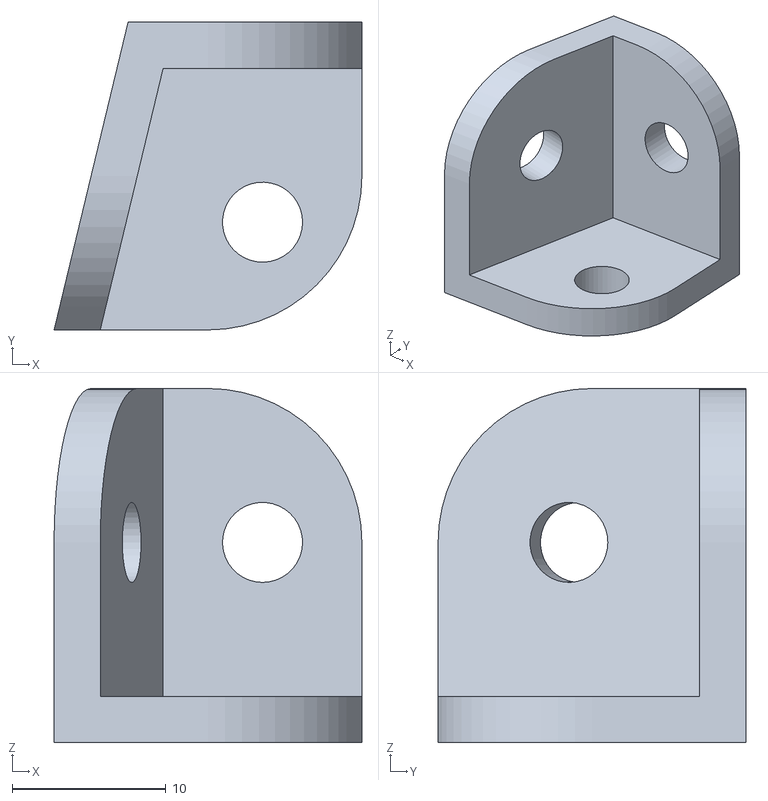
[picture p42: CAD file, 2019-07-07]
Fabrication/3D printing/enclouser/Ecerre_coin_big.STL
20.0 x 20.0 x 23.0

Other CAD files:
CAD/electronic box/Harness_1-Mega&Ramps.sldasm
CAD/3DPrint_Tool/xgentec-bowden-extruder-1.snapshot.2/Bowden Assembly.SLDASM
Fabrication/3D printing/Spool holder/Printer_mount_V2.STL
Fabrication/3D printing/Tool Holder +support.stl
CAD/3DPrint_Tool/Extruder Housing.SLDPRT
CAD/3DPrint_Tool/Mors Mobile_Extruder .sldprt
CAD/3DPrint_Tool/Pneumatic Connector 4-1_8PT v2.step
CAD/3DPrint_Tool/Pneumatic Connector.SLDPRT
CAD/3DPrint_Tool/Spool holder/Solidworks_files_V2/Long Tube V2.SLDPRT
CAD/3DPrint_Tool/Spool holder/Solidworks_files_V2/M8 Nut.SLDPRT
CAD/3DPrint_Tool/Spool holder/Solidworks_files_V2/M8 threaded rod.SLDPRT
CAD/3DPrint_Tool/Spool holder/Solidworks_files_V2/Plastic Bearing.SLDPRT
CAD/3DPrint_Tool/Spool holder/Solidworks_files_V2/Printer mount V2.SLDPRT
CAD/3DPrint_Tool/Spool holder/Solidworks_files_V2/Spool Nut.SLDPRT
CAD/3DPrint_Tool/Spool holder/Solidworks_files_V2/Spool.SLDPRT
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

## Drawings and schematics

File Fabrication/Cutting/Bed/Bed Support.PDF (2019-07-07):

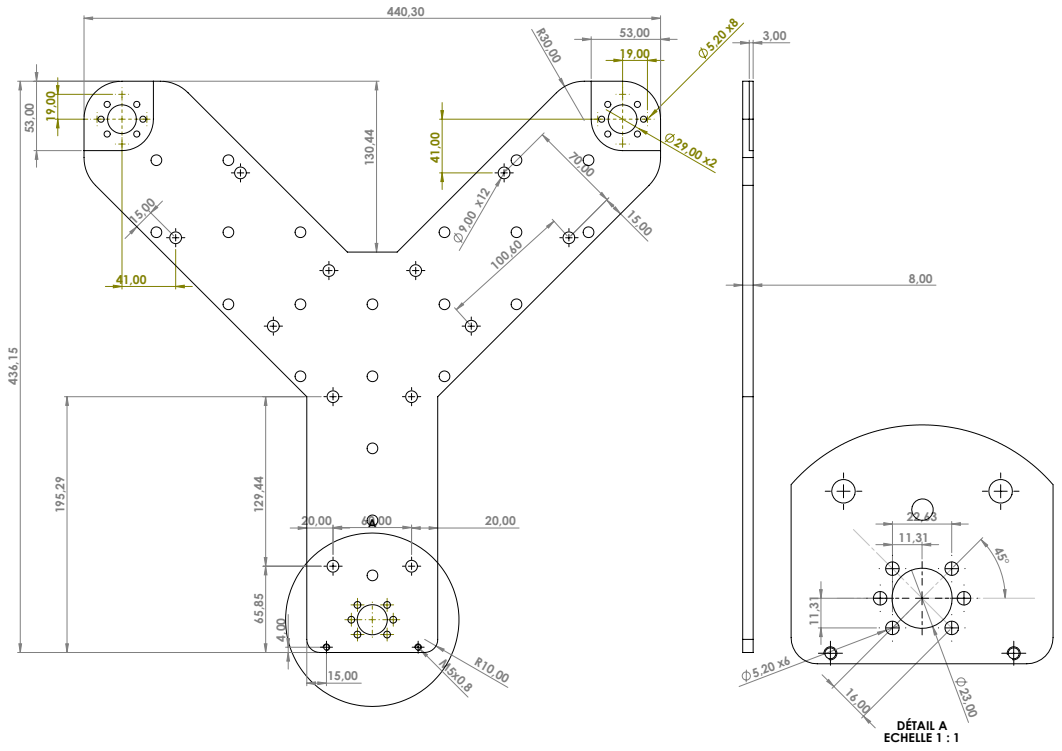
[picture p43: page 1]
DÉTAIL A ECHELLE 1 : 1

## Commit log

2019-07-07 adding CAD&Fabrication folder
    [3Dprint tool.stl, Back panel.DXF, Back panel.sldprt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]
2019-07-07 Step files
    [3DPrint_tool.SLDASM, Adjust Mount.SLDPRT, Arm.SLDPRT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]
2022-03-02 New config updates Marlin 2.0.xx
2022-03-02 upload new tft stl file for further updates
    [TFT BOX for MKS_TFT32.stl]
